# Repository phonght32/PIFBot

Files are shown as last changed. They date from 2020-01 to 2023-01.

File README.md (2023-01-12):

# PIFBot
  
### 1. Overview 

PIFBot is a ROS-based mobile robot for running SLAM (Simultaneous Localization and Mapping) algorithms to build a map and driving around this map. This robot is primarily equiped LiDAR, RGB-D camera and odometer sensors that makes it compatible with many SLAM methods. The PIFBot can be customized in various ways depending on how you reconstruct mechanical parts and use optional parts such as sensors and the computer to meet many different purposes. 

### 2. Requirement

#### 2.1. Ubuntu 16.04 Xenial
Ubuntu has been the primary platform for ROS. The releases is available to download from [Ubuntu home page.](https://ubuntu.com/)

#### 2.2. ROS Kinetic
This project uses ROS Kinetic that compatible with Ubuntu 16.04 (Xenial) to have better support from ROS community. Follow this [link](http://wiki.ros.org/kinetic) to see the installation instructions. 

#### 2.3. STM-IDF (STM32 Integrated Developement Framework)
[STM-IDF](https://github.com/phonght32/stm-idf) is an open source framework for STM32 that using C/C++ programming languague. The majority of the components in STM-IDF are available in [Github Repository](https://github.com/phonght32) under the MIT license. 

### 3. Mobile base control

Main controller board for PIFBot is OpenSTM32. The OpenSTM32 board is developed for ROS embedded systems to provide completely open source hardware and software. Everything about the board; Schematic, PCB Gerber, BOM and the firmware source code for PIFBot are available in [Github Repository](https://github.com/phonght32/openSTM32F4_LQFP64) and free to distribute under MIT license. 

The STM32F4 series is a main chip inside the OpenSTM32 board which is based on a very powerful ARM Cortex-M4 with Floating Point Unit (FPU). The developement environment for OpenSTM32 is wide open but STM-IDF which mentioned above is selected as main programming tool. 

OpenSTM32 provides digital and analog input/output pins that can interface with extension board or various sensors. 9-DOF IMU MPU9250 is available to make this board capable of processing complex motion fusion algorithms. OpenSTM32 features various communication interfaces: SPI, I2C, UART, I2S for other embedded devices. 

OpenSTM32 will be the best solution for implementing your embedded control design.

#### 3.1. Schematic
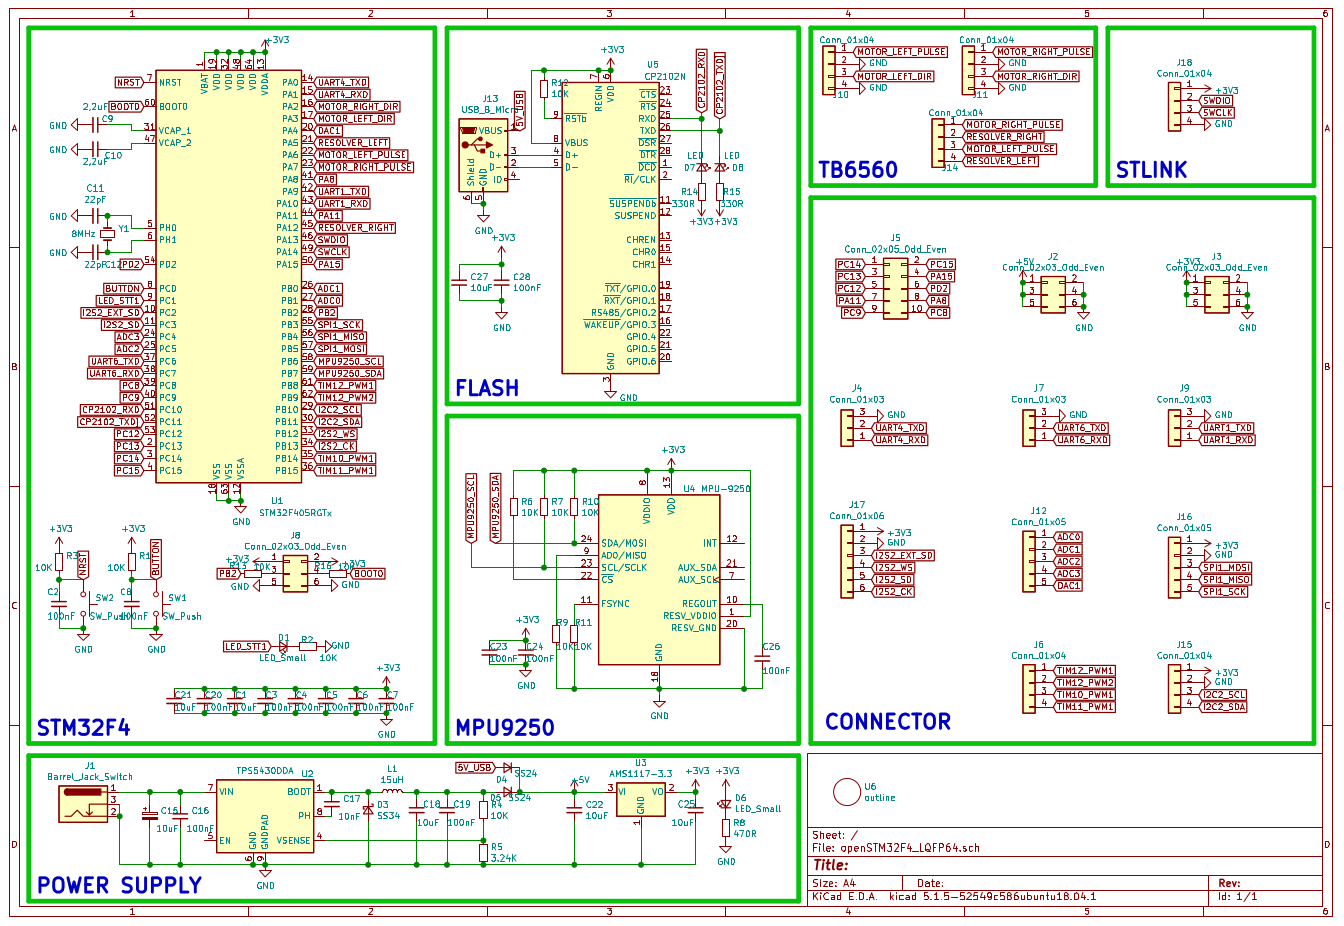
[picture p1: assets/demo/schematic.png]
schematic


#### 3.2. openSTM32 Board
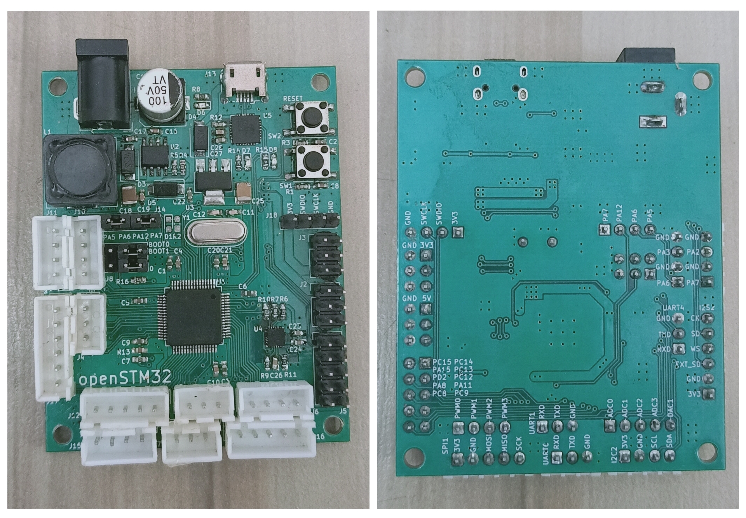
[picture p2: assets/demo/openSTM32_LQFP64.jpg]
openSTM32_LQFP64
 

### 4. Hardware assembly

Differential drive which is the most common mobile robot model is applied to PIFBot. The shape of the robot is selected as circle with two driving wheels and two caster wheels. Design in this way make the robot easy to move according to control commands. 

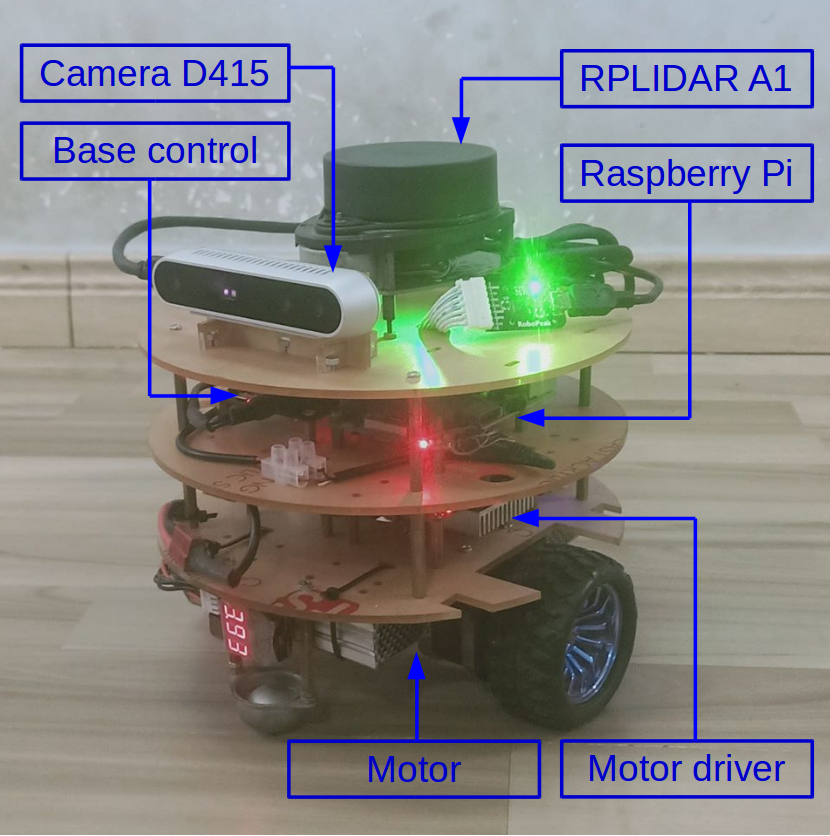
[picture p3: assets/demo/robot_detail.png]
robot_detail


This table shows many important size specifications of PIFBot. 

| Specification | Dimension |
|---|---|
| Chassis diameter | 200 mm |
| Maximum height | 212 mm |
| Wheel diameter | 65 mm |
| Axle distance | 165 mm |

#### 4.1. Chassis
PIFBot's chassis is made of mica. The chassis is designed in the way so that make it easy to carry optional parts as well as sensors. DXF files is available in this repository for laser cutting or CNC.

#### 4.2. Motor control and wheels
TB6560 stepper motor driver is used for controlling 42x42 mm stepper motor which working as actuator element. The PIFBot consists of two 65mm diameter fixed powered wheels mounted on the left and right side of the robot platform. Two castor wheels is used for balance and stability. 

#### 4.3. Single Board Computer
The Single Board Computer (SBC) is required to be able to install Linux ROS that provides the ability to use PIFBot's feature. There are various type of SBC, but Raspberry Pi 3 B+ is selected as main computer for PIFBot. 

#### 4.4. Controller Board
Calculating odometry data and controlling robot's motion are the essential requirements of controller board. The OpenSTM32 is designed to meet this requirements. There are also many available connectors in this board that make it suitable for various sensors or other applications. 

#### 4.5. Sensors
**RPLIDAR A1**  
360 Laser Range Finding RPLIDAR A1 is a 2D laser scanner capable of sensing 360 degrees that collects a set of data around the robot to use for SLAM (Simultaneous Localization and Mapping) and Navigation. It supportsnUSB interface and is easy to install on a PC. 

**Intel RealSense D415**  
The Intel RealSense D415 camera is a USB 3.0 device that can provide color, depth and infrared video streams. PIFBot adopts this camera to enable 3D SLAM and Navigation, and it is possible to apply various applications such as gesture recognition, object recognition and scene recognition based on 3D depth information obtained using RealSense Tecnology. 

#### 4.6. Power supply
OpenSTM32 controller board has both a 5V power and a 12V power, which are used in Raspberry Pi. DC/DC Buck Converter LM2596 is used for taking 11.1V from 3 cell lipo baterry and converting it into 5V that can power controller board and SBC.

### 5. System design

The system is seperated into two parts: ROS and base control. SBC receives data that collected from RPLIDAR A1 and Intel RealSense D415 camera to publish to ROS's topics. ROS's topics are owned by ROS Master so PC also implement publisher and subscriber to topics which contains data published from SBC. PC runs SLAM algorithms and Navigation, then publish motion commands to topic that manages robot's velocity (both angular and linear velocity). The motion command will be sent to controller board over rosserial protocol so that robot can build the map and drive around in this map. Simultaneously, controller board calculates robot's odometry data and feeds backward to ROS Server.

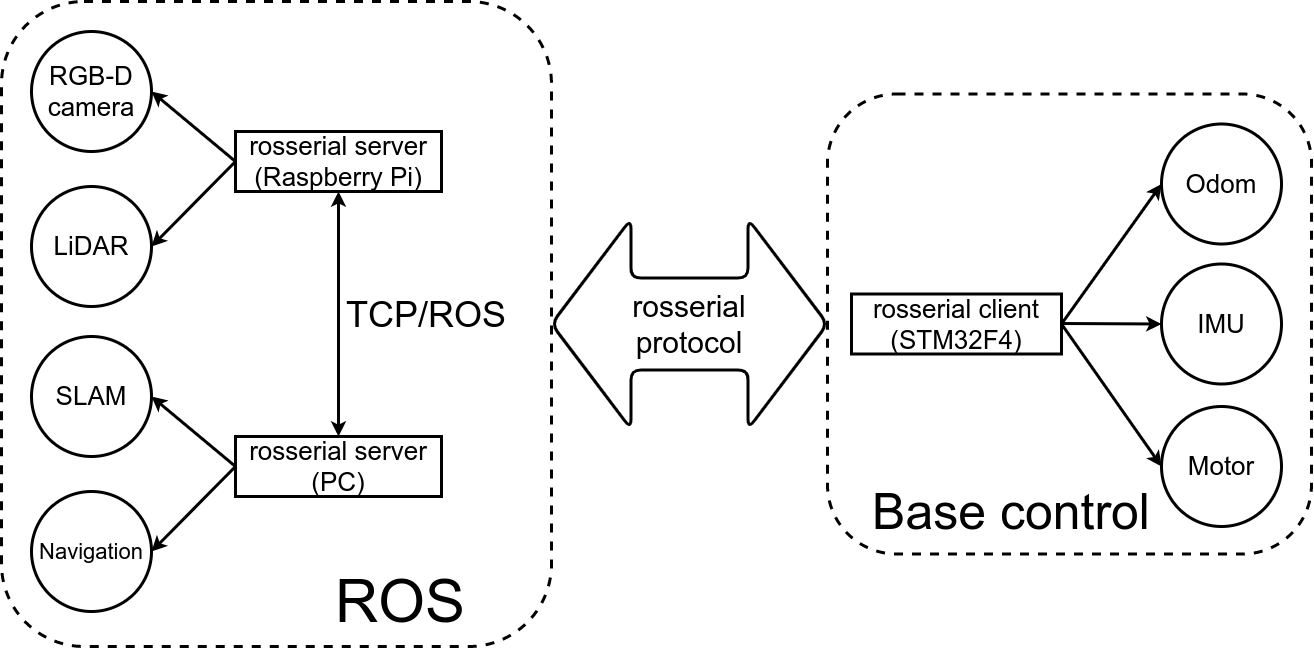
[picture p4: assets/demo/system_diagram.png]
system_diagram


### 6. Result
Real-Time Appearance-Based Mapping is used for practing SLAM and Navigation. 

#### 6.1. SLAM
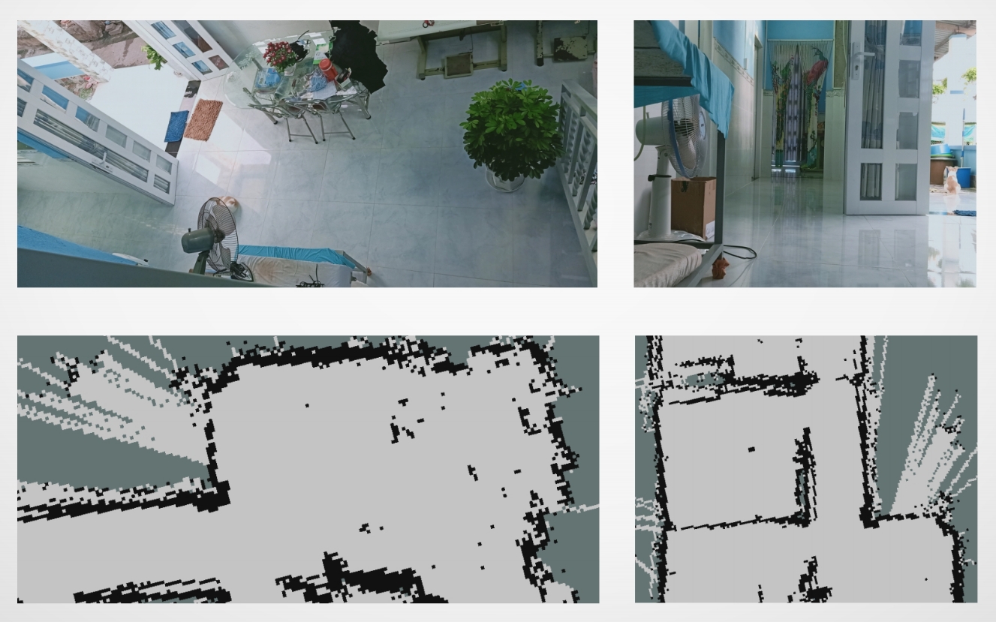
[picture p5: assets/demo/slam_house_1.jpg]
slam_house_1

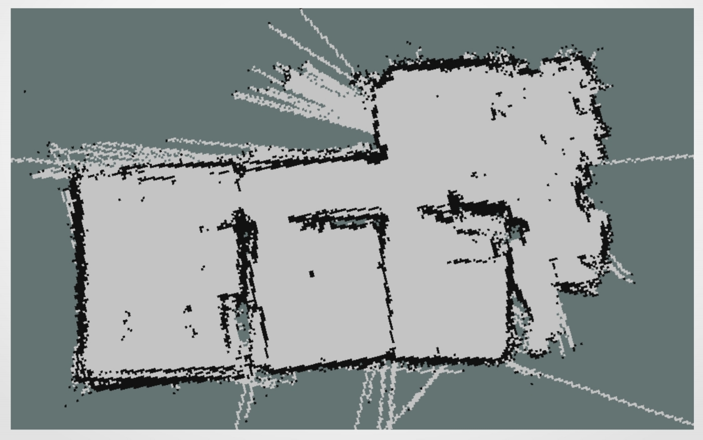
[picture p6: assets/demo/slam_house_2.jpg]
slam_house_2


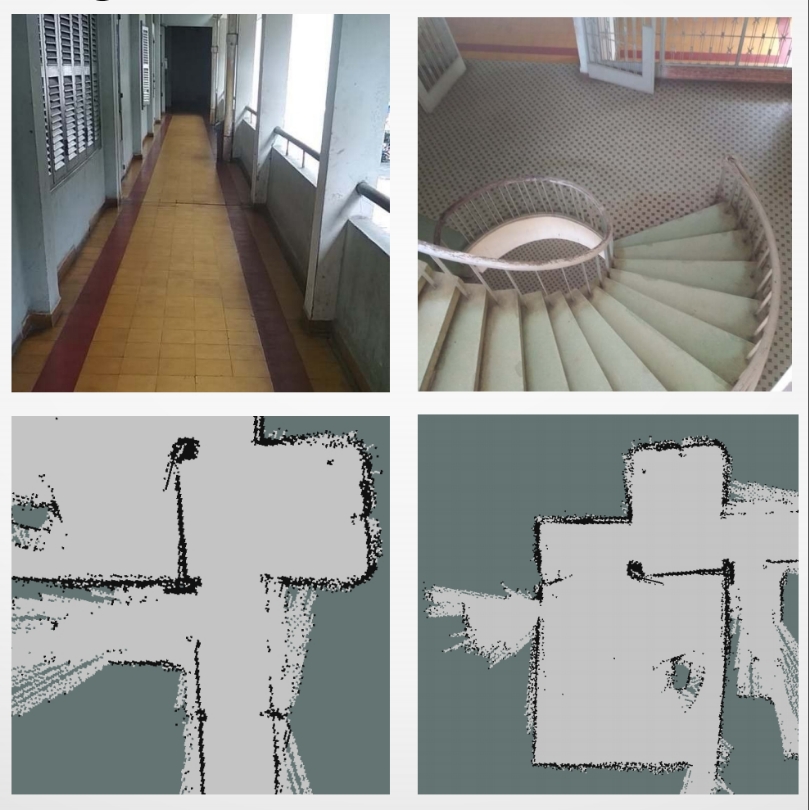
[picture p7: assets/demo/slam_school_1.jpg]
slam_school_1

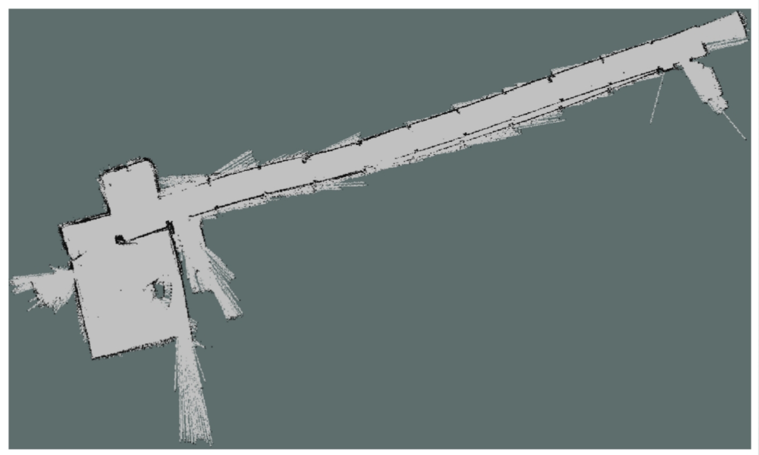
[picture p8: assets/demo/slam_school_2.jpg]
slam_school_2


#### 6.2. Navigation
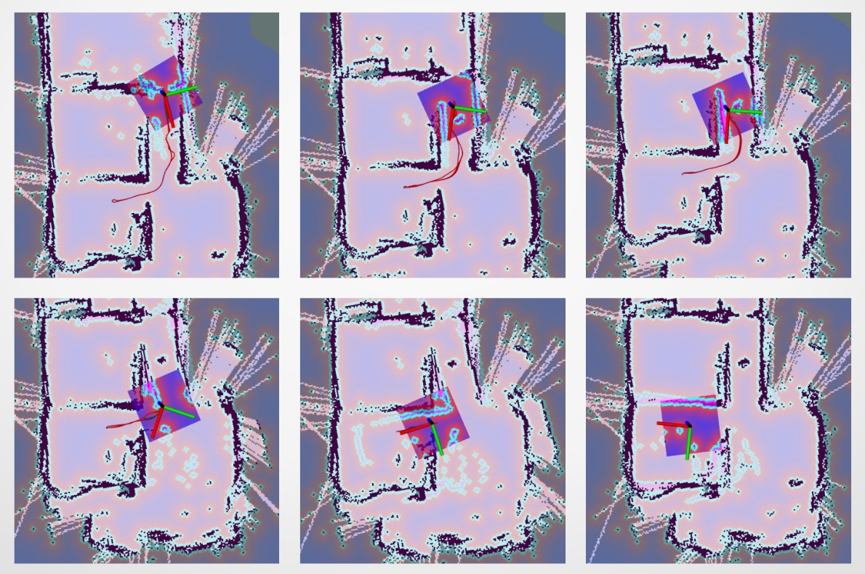
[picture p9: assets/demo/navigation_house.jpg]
navigation_house


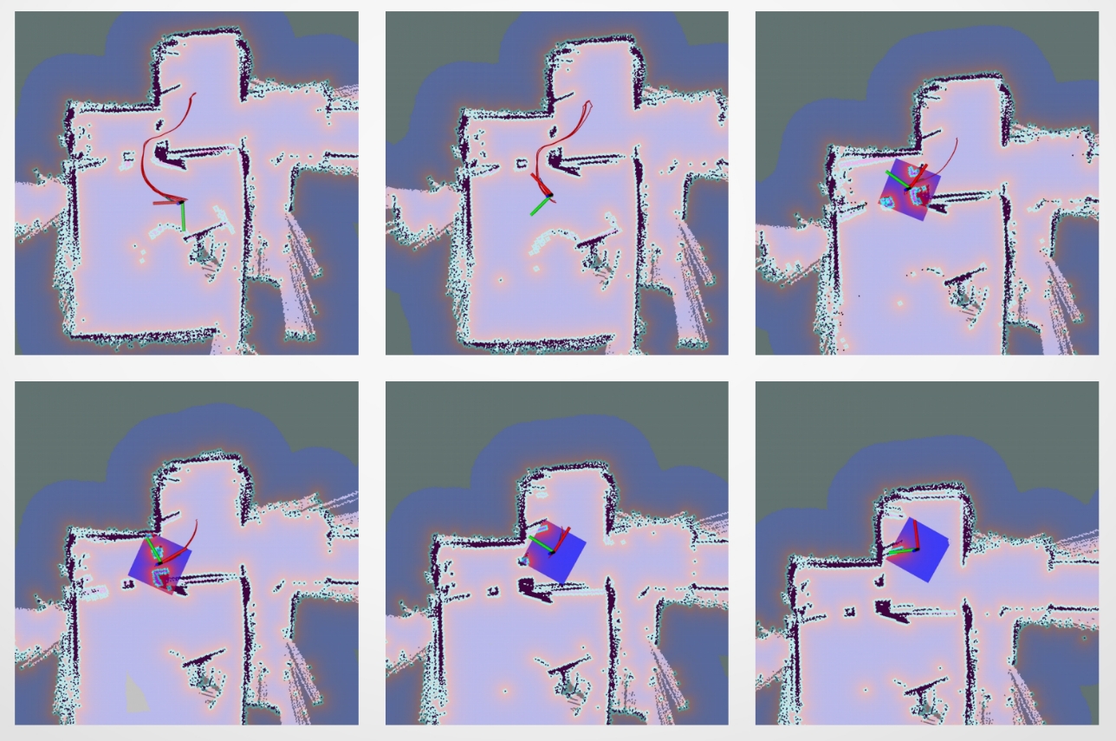
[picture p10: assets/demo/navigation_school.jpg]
navigation_school


#### 6.3. Loop-closed detection
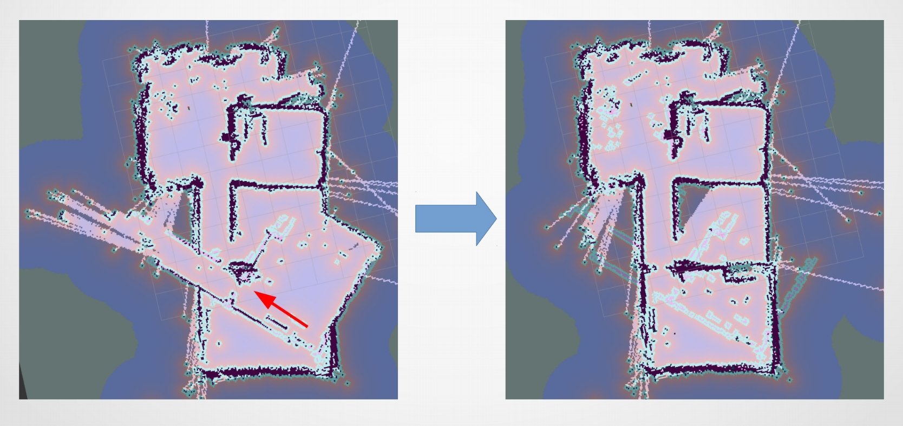
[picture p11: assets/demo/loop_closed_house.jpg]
loop_closed_house


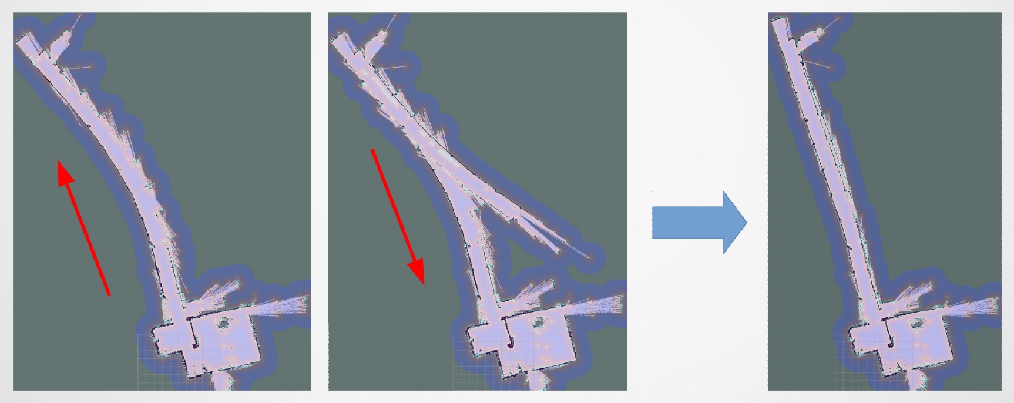
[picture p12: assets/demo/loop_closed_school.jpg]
loop_closed_school


#### 6.4. Multi-session SLAM 
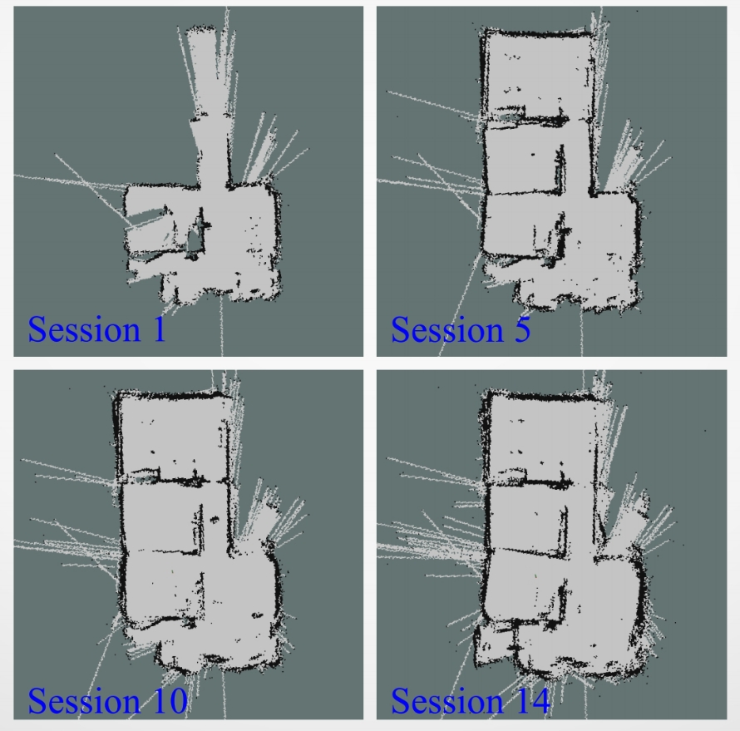
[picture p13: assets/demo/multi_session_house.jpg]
multi_session_house


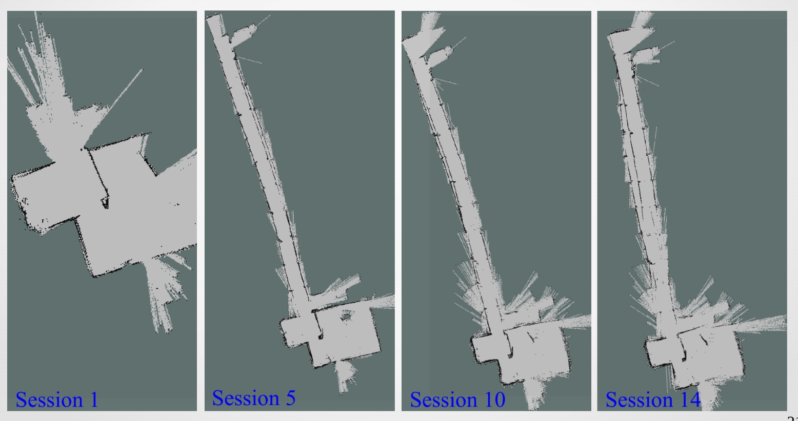
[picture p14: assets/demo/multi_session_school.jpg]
multi_session_school


#### 6.5 Video
Follow [this link](https://youtu.be/UWhPCQyU918) to watch video on Youtube. 

#### 7. Problem
For any problems, please report to [Issues](https://github.com/phonght32/PIFBot/issues) or contact email thanhphongho1998@gmail.com

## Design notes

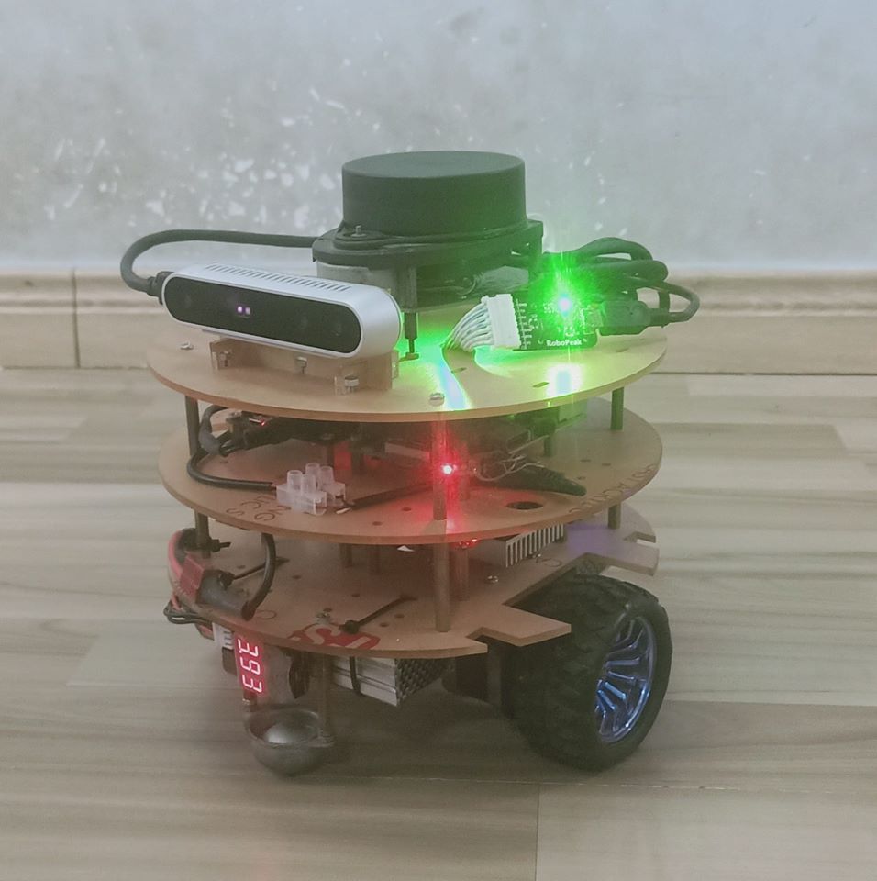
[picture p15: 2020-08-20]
assets/demo/real_robot.jpg

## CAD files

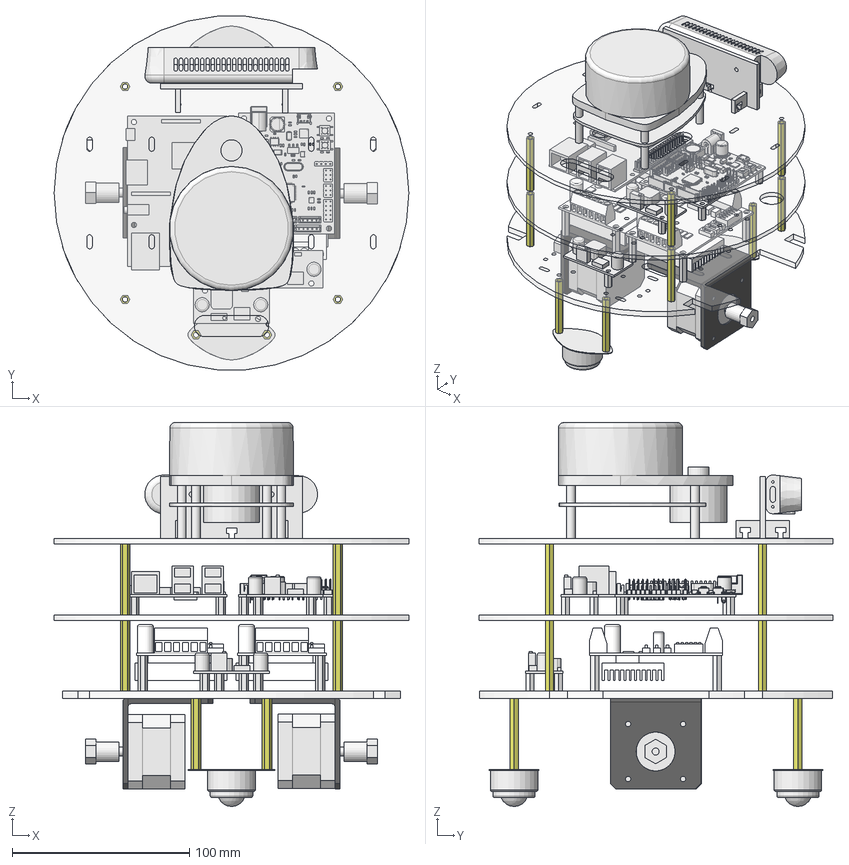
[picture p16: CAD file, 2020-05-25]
mechanical/assembly/robot_base.fcstd
200.0 x 199.3 x 216.5 mm
layer1_01
step_motor_42mm_01
step_motor_42mm_02
step_motor_42mm_bracket_01
step_motor_42mm_bracket_02
motor_flexible_coupling_connector_L18_M5_01
motor_flexible_coupling_connector_L18_M5_02
coxial_M3_40mm_01
coxial_M3_40mm_02
coxial_M3_40mm_03
coxial_M3_40mm_04
ball_transfer_01
ball_transfer_02
coxial_M3_20mm_01
coxial_M3_20mm_02
coxial_M3_20mm_03
coxial_M3_20mm_04
coxial_M3_20mm_05
coxial_M3_20mm_06
coxial_M3_20mm_07
coxial_M3_20mm_08
stepmotor_driver_tb6560_01
stepmotor_driver_tb6560_02
coxial_M3_10mm_01
coxial_M3_10mm_02
buck_converter_lm2596_01
layer2_01
coxial_M3_40mm_05
coxial_M3_40mm_06
coxial_M3_40mm_07
coxial_M3_40mm_08
coxial_M3_10mm_03
coxial_M3_10mm_04
coxial_M3_10mm_05
coxial_M3_10mm_06
coxial_M3_10mm_07
coxial_M3_10mm_08
coxial_M3_10mm_09
coxial_M3_10mm_10
coxial_M3_10mm_11
coxial_M3_10mm_12
buck_converter_lm2596_02
openSTM32F4_LQFP64_001
raspberry_pi_3Bplus_01
layer3_01
coxial_M3_40mm_09
coxial_M3_40mm_10
coxial_M3_40mm_11
coxial_M3_40mm_12
rplidar_a1_01
camera_holder_front_01
camera_holder_01
camera_holder_02
intel_realsense_d415_01

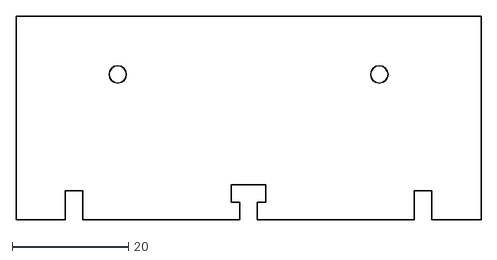
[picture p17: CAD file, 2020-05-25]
mechanical/assets/dxf/camera_holder_front.dxf
80.0 x 35.0

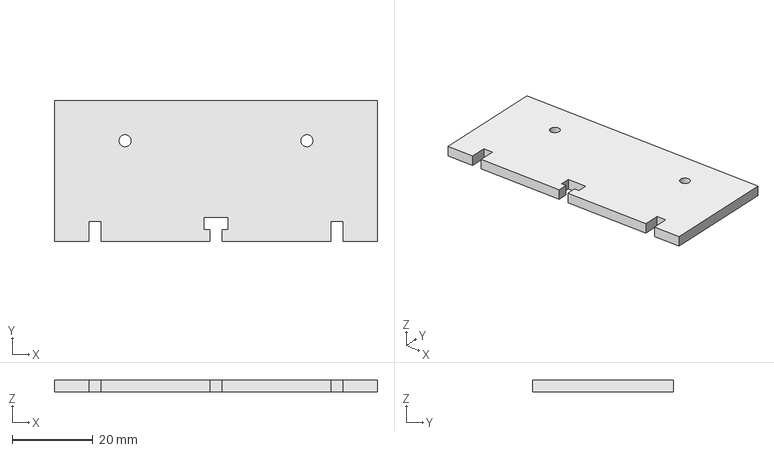
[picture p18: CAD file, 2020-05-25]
mechanical/camera_holder_front.FCStd
80.0 x 35.0 x 3.00 mm

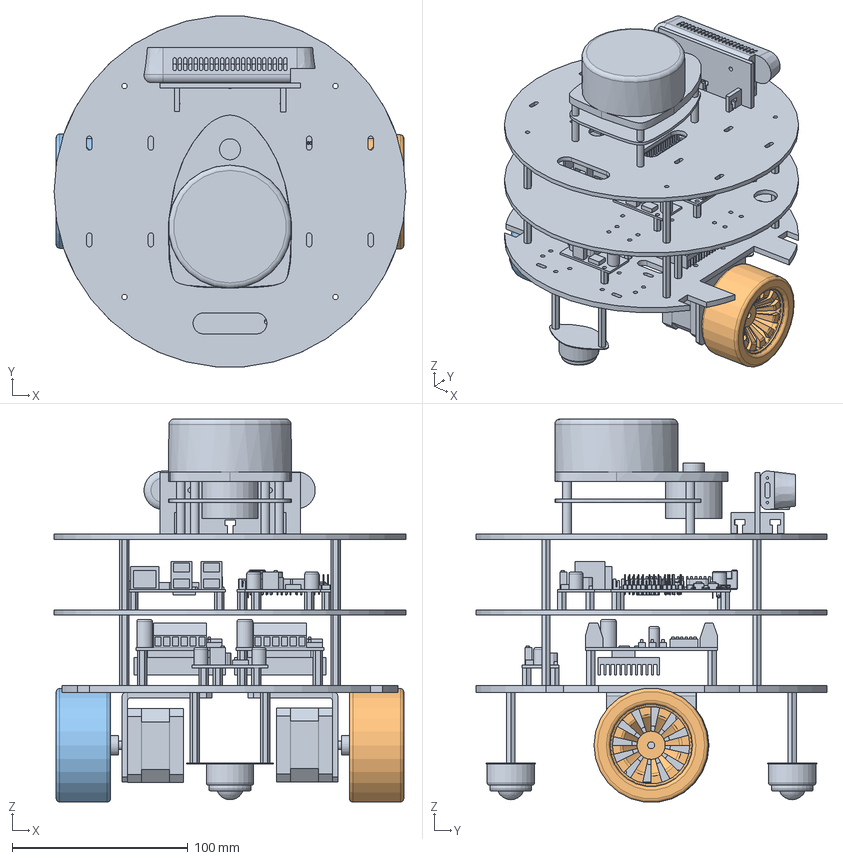
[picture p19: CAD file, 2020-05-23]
mechanical/assembly/robot.fcstd
200.0 x 199.3 x 217.8 mm
robot_base_01
robot_wheel_01
robot_wheel_02

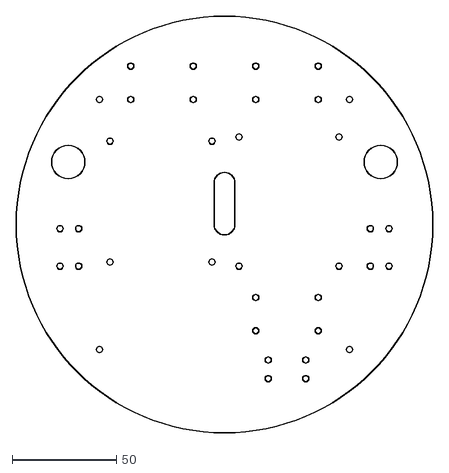
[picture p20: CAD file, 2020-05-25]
mechanical/assets/dxf/layer2.dxf
200.0 x 200.0

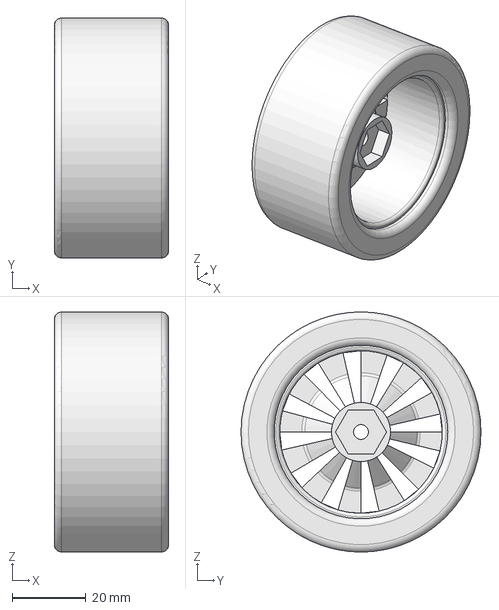
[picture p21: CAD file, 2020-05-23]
mechanical/assembly/robot_wheel.fcstd
31.0 x 65.0 x 65.0 mm

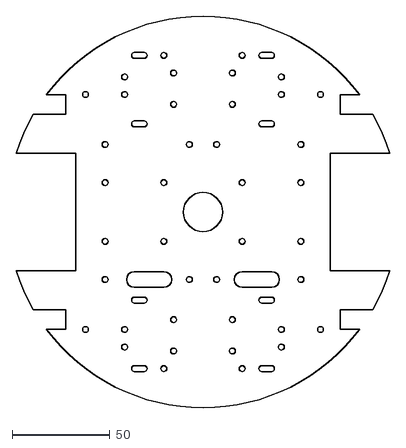
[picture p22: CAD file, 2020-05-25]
mechanical/assets/dxf/layer1.dxf
190.8 x 200.0

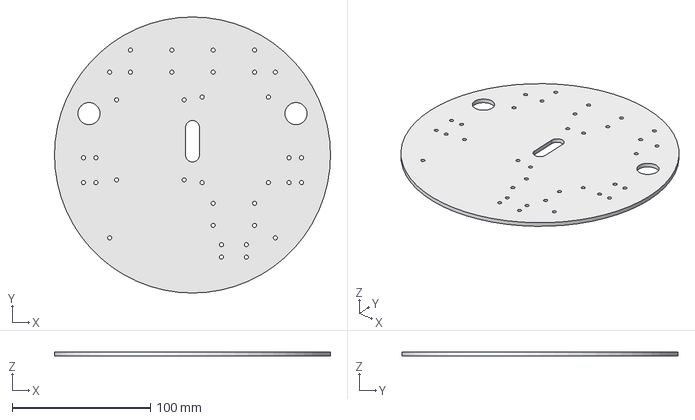
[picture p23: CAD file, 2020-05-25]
mechanical/layer2.FCStd
200.0 x 200.0 x 3.00 mm

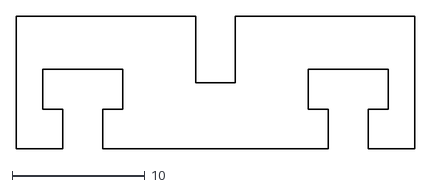
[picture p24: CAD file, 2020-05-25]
mechanical/assets/dxf/camera_holder.dxf
30.0 x 10.0

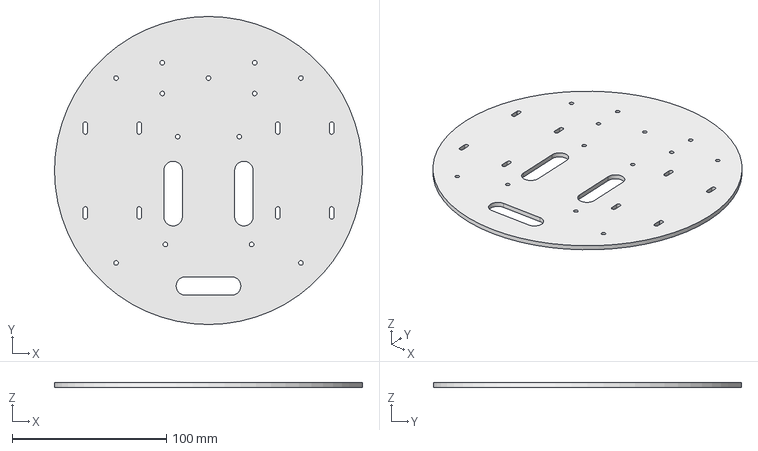
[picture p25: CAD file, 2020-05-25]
mechanical/layer3.FCStd
200.0 x 200.0 x 3.00 mm

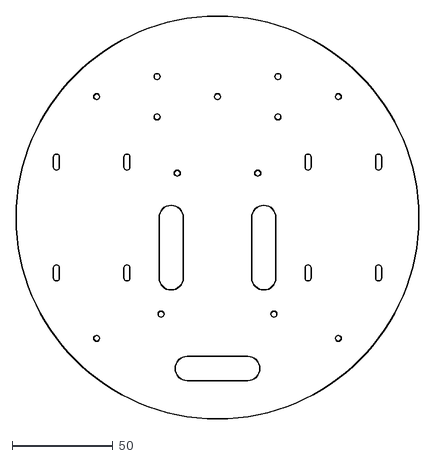
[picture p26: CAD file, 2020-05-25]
mechanical/assets/dxf/layer3.dxf
200.0 x 200.0

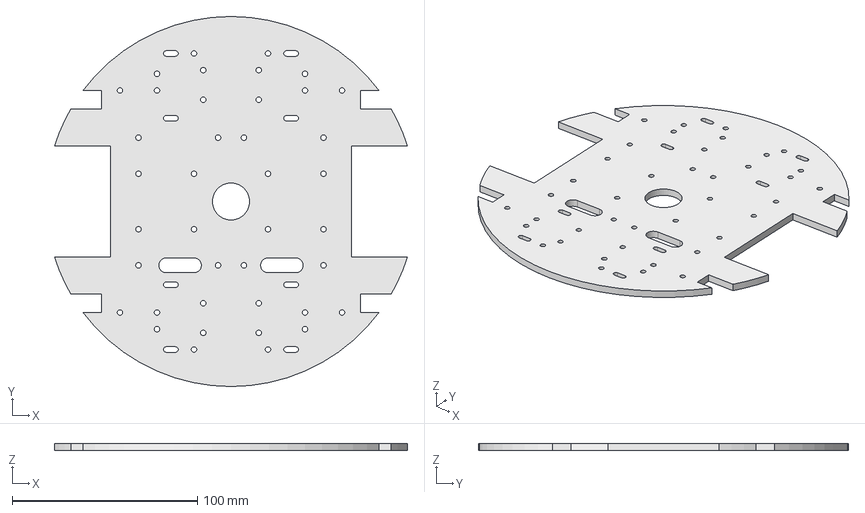
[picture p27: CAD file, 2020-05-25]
mechanical/layer1.FCStd
190.8 x 200.0 x 4.00 mm

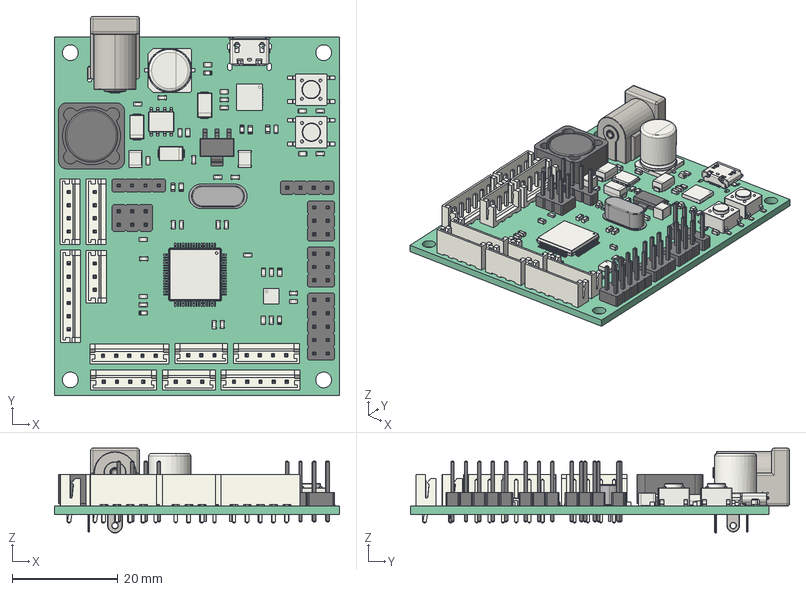
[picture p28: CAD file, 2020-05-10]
mechanical/openSTM32F4_LQFP64.FCStd
54.0 x 71.9 x 16.1 mm
Pcb_d8e2
J1_User Library-K375A -PCM DC Power Jack 2mm Pin_5EA4031C
J5_PinHeader_2x05_P254mm_Vertical_5EB08CC2
J18_PinHeader_1x04_P254mm_Vertical_5EB0AE7D
R16_R_0603_1608Metric_5EAFAF91
R13_R_0603_1608Metric_5EAFF99B
U4_QFN-24-1EP_3x3mm_Pitch0.4mm_5EA5C3D2
J3_PinHeader_2x03_P254mm_Vertical_5EA40313
J2_PinHeader_2x03_P254mm_Vertical_5EA402F7
J9_JST_B3B_EH_A_5EA3E20C
J7_JST_B3B_EH_A_5EA3E1B5
J4_JST_B3B_EH_A_5EA3E114
J14_PinHeader_1x04_P254mm_Vertical_5EAC9FAF
J8_PinHeader_2x03_P254mm_Vertical_5EAAB127
C21_C_0603_1608Metric_5EA43EF0
D4_D_SMA_5EA284CE
D3_D_SMA_5EB50787
D5_D_SMA_5EA30606
Y1_Crystal_HC49-4H_Vertical_5EA9EA10
C18_C_1210_3225Metric_5EA436E9
C25_C_1210_3225Metric_5EA31A7E
C15_CP_Elec_8x10_5EA2560F
J13_USB_Micro-B_Molex_47346-0001_5EA50851
U5_QFN-28-1EP_5x5mm_Pitch0.5mm_5EA4E590
U3_SOT_223_5EA53A3F
U2_HTSOP_8_1EP_39x49mm_Pitch127mm_5EA0849D
U1_LQFP_64_10x10mm_P05mm_5EA24989
SW2_SW_SPST_PTS645_5EB7520E
SW1_SW_SPST_PTS645_5EA3CB54
R15_R_0603_1608Metric_5EA083D6
R14_R_0603_1608Metric_5EA083C5
R12_R_0603_1608Metric_5EA4105A
R11_R_0603_1608Metric_5EA24C1D
R10_R_0603_1608Metric_5EA5C4B6
R9_R_0603_1608Metric_5EA2483F
R8_R_0603_1608Metric_5EA9B3FB
R7_R_0603_1608Metric_5EA5C456
R6_R_0603_1608Metric_5EA5C378
R5_R_0603_1608Metric_5EA0832C
R4_R_0603_1608Metric_5EA0831B
R3_R_0603_1608Metric_5EA0830A
R2_R_0603_1608Metric_5EAD2415
R1_R_0603_1608Metric_5EA082E8
L1_L_Wuerth_MAPI_3012_5EA24663
L1_SRR1260_5EA24663[2]
J17_JST_B6B_EH_A_5EA2A89C
J16_JST_B5B_EH_A_5EA0824F
J15_JST_B4B_EH_A_5EA0822C
J12_JST_B5B_EH_A_5EA3C541
J11_JST_B4B_EH_A_5EA26EEF
J10_JST_B4B_EH_A_5EA0819C
J6_JST_B4B_EH_A_5EA08116
D8_LED_0603_1608Metric_5EB538CC
D7_LED_0603_1608Metric_5EA08010
D6_LED_0603_1608Metric_5EA9B42D
D1_LED_0603_1608Metric_5EA07F8A
C28_C_0603_1608Metric_5EA4F23B
C27_C_0603_1608Metric_5EA4F26B
C26_C_0603_1608Metric_5EA24BED
C24_C_0603_1608Metric_5EA83DF3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

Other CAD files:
mechanical/camera_holder.FCStd

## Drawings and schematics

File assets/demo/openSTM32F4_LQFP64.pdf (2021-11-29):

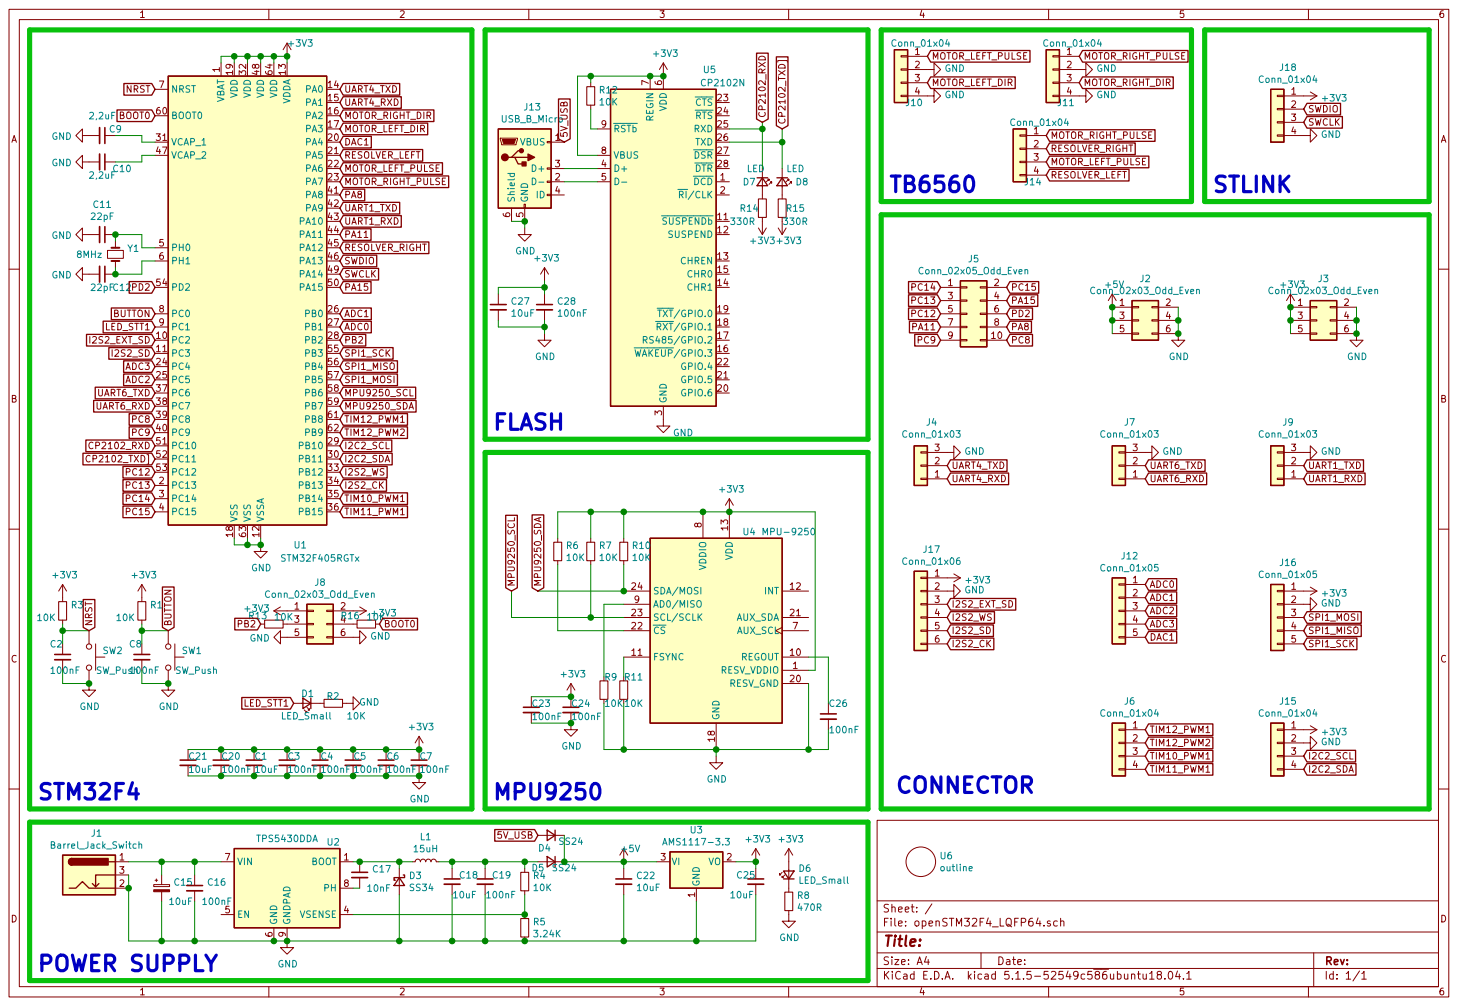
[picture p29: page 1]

1 VCAP_1 31 VCAP_2 47 VDD 19 VDD 32 VDD 48 VDD 64 VDDA 13 VSS 18 VSS 63 VSSA 12 U1 STM32F405RGTx BUTTON
PD2 BOOT0

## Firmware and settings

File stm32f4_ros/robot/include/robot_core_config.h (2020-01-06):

#ifndef _ROBOT_CORE_CONFIG_H_
#define _ROBOT_CORE_CONFIG_H_

//#include "stdint.h"

#include <ros.h>
#include <ros/time.h>
#include <std_msgs/Bool.h>
#include <std_msgs/Empty.h>
#include <std_msgs/Int32.h>
#include <std_msgs/String.h>
#include <std_msgs/UInt16.h>
#include <sensor_msgs/Imu.h>
#include <sensor_msgs/JointState.h>
#include <sensor_msgs/BatteryState.h>
#include <sensor_msgs/MagneticField.h>
#include <geometry_msgs/Vector3.h>
#include <geometry_msgs/Twist.h>
#include <tf/tf.h>
#include <tf/transform_broadcaster.h>
#include <nav_msgs/Odometry.h>

#include <robot_model_param.h>

#define CONTROL_MOTOR_SPEED_FREQUENCY          30   //hz
#define CONTROL_MOTOR_TIMEOUT                  500  //ms
#define IMU_PUBLISH_FREQUENCY                  200  //hz
#define CMD_VEL_PUBLISH_FREQUENCY              30   //hz
#define DRIVE_INFORMATION_PUBLISH_FREQUENCY    30   //hz
#define VERSION_INFORMATION_PUBLISH_FREQUENCY  1    //hz
#define DEBUG_LOG_FREQUENCY                    10   //hz

#define WHEEL_NUM                        2

#define LEFT                             0
#define RIGHT                            1

#define LINEAR                           0
#define ANGULAR                          1

#define DEG2RAD(x)                       (x * 0.01745329252)  // *PI/180
#define RAD2DEG(x)                       (x * 57.2957795131)  // *180/PI

#define TICK2RAD                         0.001533981  // 0.087890625[deg] * 3.14159265359 / 180 = 0.001533981f

#define TEST_DISTANCE                    0.300     // meter
#define TEST_RADIAN                      3.14      // 180 degree

// #define DEBUG
#define DEBUG_SERIAL                     SerialBT2


void commandVelocityCallback(const geometry_msgs::Twist& cmd_vel_msg);
void resetCallback(const std_msgs::Empty &reset_msg);

void publishCmdVelFromMotorMsg(void);
void publishImuMsg(void);
void publishDriveInformation(void);

ros::Time rosNow(void);
ros::Time addMicros(ros::Time &t, uint32_t _micros);

void updateVariable(bool isConnected);
void updateMotorInfo(int32_t left_tick, int32_t right_tick);
void updateTime(void);
void updateOdometry(void);
void updateJoint(void);
void updateJointStates(void);
void updateTF(geometry_msgs::TransformStamped& odom_tf);
void updateGyroCali(bool isConnected);
void updateGoalVelocity(void);
void updateTFPrefix(bool isConnected);

void initOdom(void);
void initJointStates(void);

bool calcOdometry(double diff_time);

void sendLogMsg(void);
void waitForSerialLink(bool isConnected);


/*******************************************************************************
* ROS NodeHandle
*******************************************************************************/
ros::NodeHandle nh;
ros::Time current_time;
uint32_t current_offset;

/*******************************************************************************
* ROS Parameter
*******************************************************************************/
char get_prefix[10];
char *get_tf_prefix = get_prefix;

char odom_header_frame_id[30];
char odom_child_frame_id[30];

char imu_frame_id[30];

char joint_state_header_frame_id[30];

/*******************************************************************************
* Subscriber
*******************************************************************************/
ros::Subscriber<geometry_msgs::Twist> cmd_vel_sub("cmd_vel", commandVelocityCallback);

ros::Subscriber<std_msgs::Empty> reset_sub("reset", resetCallback);

/*******************************************************************************
* Publisher
*******************************************************************************/
sensor_msgs::Imu imu_msg;
ros::Publisher imu_pub("imu", &imu_msg);

geometry_msgs::Twist cmd_vel_motor_msg;
ros::Publisher cmd_vel_motor_pub("cmd_vel_motor", &cmd_vel_motor_msg);

nav_msgs::Odometry odom;
ros::Publisher odom_pub("odom", &odom);

sensor_msgs::JointState joint_states;
ros::Publisher joint_states_pub("joint_states", &joint_states);

sensor_msgs::BatteryState battery_state_msg;
ros::Publisher battery_state_pub("battery_state", &battery_state_msg);

/*******************************************************************************
* Transform Broadcaster
*******************************************************************************/
geometry_msgs::TransformStamped odom_tf;
tf::TransformBroadcaster tf_broadcaster;

/*******************************************************************************
* SoftwareTimer of Robot
*******************************************************************************/
static uint32_t tTime[10];

/*******************************************************************************
* Calculation for odometry
*******************************************************************************/
bool init_encoder = true;
int32_t last_diff_tick[WHEEL_NUM] = {0, 0};
double last_rad[WHEEL_NUM] = {0.0, 0.0};
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

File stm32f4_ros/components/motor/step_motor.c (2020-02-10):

#include "include/step_motor.h"

#define PWM_DUTYCYCLE_DEFAULT	30

typedef struct step_motor {
    pwm_handle_t clk_handle;
    gpio_handle_t dir_handle;
} step_motor_t;

static void step_motor_cleanup(step_motor_handle_t handle)
{
	free(handle->dir_handle);
	free(handle->clk_handle);
	free(handle);
}

step_motor_handle_t step_motor_init(step_motor_config_t *config)
{
    step_motor_handle_t handle;
    if( (handle             = calloc(1, sizeof(step_motor_t))) &&
        (handle->clk_handle = calloc(1, sizeof(pwm_handle_t)))  &&
        (handle->dir_handle = calloc(1, sizeof(gpio_handle_t))) == NULL )
    {
    	step_motor_cleanup(handle);
        return -1;
    }

    handle->clk_handle = pwm_init(&config->pin_clk);
    handle->dir_handle = gpio_init(&config->pin_dir);
    pwm_set_duty(handle->clk_handle, PWM_DUTYCYCLE_DEFAULT);

    return handle;
}

int step_motor_start(step_motor_handle_t handle)
{
	pwm_start(handle->clk_handle);

	return 0;
}

int step_motor_stop(step_motor_handle_t handle)
{
	pwm_stop(handle->clk_handle);

	return 0;
}

int step_motor_set_freq(step_motor_handle_t handle, uint32_t freq_hz)
{
	pwm_set_freq(handle->clk_handle,freq_hz);

	return 0;
}

int step_motor_set_dir(step_motor_handle_t handle, bool dir)
{
	gpio_set_level(handle->dir_handle, dir);

	return 0;
}

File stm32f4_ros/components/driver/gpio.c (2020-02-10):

#include "include/gpio.h"

#define GPIO_SPEED_FREQ_DEFAULT  GPIO_SPEED_FREQ_VERY_HIGH

typedef struct gpio {
    gpio_port_t     gpio_port;
    gpio_num_t      gpio_num;
    gpio_mode_t     gpio_mode;
    gpio_reg_pull_t gpio_reg_pull;
} gpio_t;

GPIO_TypeDef *GPIOx_MAPPING[GPIO_PORT_MAX] = {
    GPIOA,
    GPIOB,
    GPIOC,
    GPIOD,
    GPIOE,
    GPIOF,
    GPIOG,
    GPIOH,
    GPIOI
};

uint16_t GPIO_PIN_x_MAPPING[GPIO_NUM_MAX] = {
    GPIO_PIN_0,
    GPIO_PIN_1,
    GPIO_PIN_2,
    GPIO_PIN_3,
    GPIO_PIN_4,
    GPIO_PIN_5,
    GPIO_PIN_6,
    GPIO_PIN_7,
    GPIO_PIN_8,
    GPIO_PIN_9,
    GPIO_PIN_10,
    GPIO_PIN_11,
    GPIO_PIN_12,
    GPIO_PIN_13,
    GPIO_PIN_14,
    GPIO_PIN_15
};

uint32_t GPIO_REG_PULL_MAPPING[GPIO_REG_PULL_MAX] = {
    GPIO_NOPULL,
    GPIO_PULLUP,
    GPIO_PULLDOWN
};

uint32_t RCC_AHB1ENR_GPIOxEN_MAPPING[GPIO_PORT_MAX] = {
    RCC_AHB1ENR_GPIOAEN,
    RCC_AHB1ENR_GPIOBEN,
    RCC_AHB1ENR_GPIOCEN,
    RCC_AHB1ENR_GPIODEN,
    RCC_AHB1ENR_GPIOEEN,
    RCC_AHB1ENR_GPIOFEN,
    RCC_AHB1ENR_GPIOGEN,
    RCC_AHB1ENR_GPIOHEN,
    RCC_AHB1ENR_GPIOIEN,
};

gpio_handle_t gpio_init(gpio_config_t *config)
{
    gpio_handle_t handle;
    handle = calloc(1, sizeof(gpio_t));
    if (handle == NULL)
    {
        return -1;
    }

    uint32_t RCC_AHB1ENR_GPIOxEN;
    uint16_t GPIO_PIN_x;
    GPIO_TypeDef *GPIOx;
    uint32_t GPIO_REG_PULL_TYPE;

    RCC_AHB1ENR_GPIOxEN = RCC_AHB1ENR_GPIOxEN_MAPPING[config->gpio_port];
    GPIO_PIN_x = GPIO_PIN_x_MAPPING[config->gpio_num];
    GPIOx = GPIOx_MAPPING[config->gpio_port];
    GPIO_REG_PULL_TYPE = GPIO_REG_PULL_MAPPING[config->gpio_reg_pull];

    do {
        __IO uint32_t tmpreg = 0x00U;
        SET_BIT(RCC->AHB1ENR, RCC_AHB1ENR_GPIOxEN);
        tmpreg = READ_BIT(RCC->AHB1ENR, RCC_AHB1ENR_GPIOxEN);
        UNUSED(tmpreg);
    } while (0U);

    GPIO_InitTypeDef GPIO_InitStruct = {0};
    if (config->gpio_mode == GPIO_INPUT)
    {
        GPIO_InitStruct.Pin = GPIO_PIN_x;
        GPIO_InitStruct.Mode = GPIO_MODE_INPUT;
        GPIO_InitStruct.Pull = GPIO_REG_PULL_TYPE;
        HAL_GPIO_Init(GPIOx, &GPIO_InitStruct);
    }
    if (config->gpio_mode == GPIO_OUTPUT)
    {
        HAL_GPIO_WritePin(GPIOx, GPIO_PIN_x, GPIO_PIN_RESET);
        GPIO_InitStruct.Pin = GPIO_PIN_x;
        GPIO_InitStruct.Mode = GPIO_MODE_OUTPUT_PP;
        GPIO_InitStruct.Pull = GPIO_REG_PULL_TYPE;
        GPIO_InitStruct.Speed = GPIO_SPEED_FREQ_DEFAULT;
        HAL_GPIO_Init(GPIOx, &GPIO_InitStruct);
    }

    handle->gpio_port     = config->gpio_port;
    handle->gpio_num      = config->gpio_num;
    handle->gpio_mode     = config->gpio_mode;
    handle->gpio_reg_pull = config->gpio_reg_pull;

    return handle;
}

int gpio_set_level(gpio_handle_t handle, uint8_t state)
{
    HAL_GPIO_WritePin(GPIOx_MAPPING[handle->gpio_port], GPIO_PIN_x_MAPPING[handle->gpio_num], state);

    return 0;
}

int gpio_toggle_level(gpio_handle_t handle)
{
    HAL_GPIO_TogglePin(GPIOx_MAPPING[handle->gpio_port], GPIO_PIN_x_MAPPING[handle->gpio_num]);

    return 0;
}

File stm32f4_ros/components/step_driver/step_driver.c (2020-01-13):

#include "stm32f4xx_hal.h"

#include "stdlib.h"

#include "include/step_driver.h"

#define PWM_DUTYCYCLE_DEFAULT	30

typedef struct step_driver {
    pwm_handle_t clk_handle;
    gpio_handle_t dir_handle;
} step_driver_t;

static void step_driver_cleanup(step_driver_handle_t handle)
{
	free(handle->dir_handle);
	free(handle->clk_handle);
	free(handle);
}

step_driver_handle_t step_driver_init(step_driver_config_t *config)
{
    step_driver_handle_t handle;
    if( (handle             = calloc(1, sizeof(step_driver_t))) &&
        (handle->clk_handle = calloc(1, sizeof(pwm_handle_t)))  &&
        (handle->dir_handle = calloc(1, sizeof(gpio_handle_t))) == NULL )
    {
    	step_driver_cleanup(handle);
        return -1;
    }

    handle->clk_handle = pwm_init(&config->pin_clk);
    handle->dir_handle = gpio_init(&config->pin_dir);
    pwm_set_duty(handle->clk_handle, PWM_DUTYCYCLE_DEFAULT);

    return handle;
}

int step_driver_start(step_driver_handle_t handle)
{
	pwm_start(handle->clk_handle);

	return 0;
}

int step_driver_stop(step_driver_handle_t handle)
{
	pwm_stop(handle->clk_handle);

	return 0;
}

int step_driver_set_freq(step_driver_handle_t handle, uint32_t freq_hz)
{
	pwm_set_freq(handle->clk_handle,freq_hz);

	return 0;
}

int step_driver_set_dir(step_driver_handle_t handle, bool dir)
{
	gpio_set_level(handle->dir_handle, dir);

	return 0;
}

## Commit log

2019-11-25 add freecad 3d models
    [assembly_chasis.FCStd, ball-transfer.FCStd, coxial-4cm.FCStd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]
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2019-11-27 add pwm_init() function
    [stm32f407 Debug.cfg]
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2019-11-28 fix params in struct config of pwm_init() and return type
    [timer.c]
2019-11-28 fix pwm_init() return value
    [timer.c]
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2019-11-28 fix pwm_start()
2019-11-28 fix pwm_set_timer_params() argument
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2019-11-28 fix TIM_OCxInit in pwm_init() function
    [timer.c]
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2019-12-01 fix HSE_VALUE in stm32f4xx.h
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2019-12-04 add dma init & dma intr enable function
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2019-12-11 fix a4988 handle structure
    [timer.c]
2019-12-16 add kicad component
    [mainboard.kicad_pcb, mainboard.sch]
2019-12-16 remove kicad mainboard project
    [mainboard.kicad_pcb, mainboard.sch]
2019-12-16 add gazebo
    [model.sdf]
2019-12-16 update 3d model
    [assembly_chasis.FCStd, model.sdf, robot_base.FCStd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]
2019-12-17 update kicad project
    [mainboard.kicad_pcb, mainboard.sch]
2019-12-17 update freecad model.sdf
    [model.sdf]
2019-12-18 update robot model
    [model.sdf, robot_base.stl, robot_wheel.stl]
2019-12-18 add turtlebot3
    [model.sdf, robot_base.stl, robot_wheel.stl]
2019-12-18 update model urdf
    [assembly_chasis.FCStd, common_properties.xacro, lds.stl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]
2019-12-18 add robot teleop
    [robot_thesis_v1_0.urdf.xacro]
2019-12-18 remove param robot model
    [robot_thesis.gazebo.xacro, robot_thesis.urdf.xacro]
2019-12-21 complete pcb
    [mainboard.kicad_pcb, mainboard.sch, mainboard_v1_0.kicad_pcb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]
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2019-12-24 fix stm rosserial
    [layer1.FCStd, mainboard_v1_0.kicad_pcb]
2019-12-25 add stm32f4 hal custom lib
    [layer1.FCStd, layer1.dxf, layer2.FCStd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]
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2019-12-28 add stm32f4 ros
    [stm32f4_hal_ros Debug.cfg]
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2019-12-28 update ros
    [stm32f407 Debug.cfg]
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2019-12-31 update uart check error
    [uart.c]
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2020-01-03 add stm32f4 project
    [stm32f4 Debug.cfg, stm32f4_hal_ros Debug.cfg]
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2020-01-07 add ros time now
    [stm32f4_ros Debug.cfg]
2020-01-09 add diode & led status
    [mainboard_v1_0.kicad_pcb, mainboard_v1_0.sch]
2020-01-13 update schematic
    [mainboard_v1_0.kicad_pcb, mainboard_v1_0.sch]
2020-01-19 fix hardware
    [mainboard_v1_0.kicad_pcb]
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2020-02-08 update robot_base model
    [assembly_chasis.FCStd, robot_base.FCStd, robot_base.stl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]
2020-02-08 update urdf description
    [lds.stl, left_tire.stl, right_tire.stl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]
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2020-02-10 remove stm32f4 project
    [stm32f4 Debug.cfg, stm32f4_hal_ros Debug.cfg]
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2020-02-10 add project file
    [mainboard_v2_0.kicad_pcb, mainboard_v2_0.sch]
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2020-03-01 fix get imu quaternion
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2020-03-08 update imu filter and fix imu sensor function
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2020-03-20 remove lidar-camera submodule
    [LidarCam.cfg]
2020-03-20 remove submodule
    [LidarCam.cfg, dynamic_range.cfg]
2020-03-20 remove submodule file
    [dynamic_range.cfg]
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2020-03-23 add camera simulation
    [robot_thesis.gazebo.xacro, robot_thesis.urdf.xacro]
2020-04-02 change robot footprint
    [robot_thesis.gazebo.xacro]
2020-04-02 fix collision in urdf description
    [robot_thesis.urdf.xacro]
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2020-04-12 fix error cannot run imu
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2020-04-21 remove stm32 firmware used sw4stm32
    [stm32f4_ros Debug.cfg]
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2020-04-21 remove hardware v2.0 folder
    [mainboard_v2_0.kicad_pcb, mainboard_v2_0.sch]
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2020-04-26 change robot simulation folder name
    [model.sdf, robot_base.stl, robot_lidar.stl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]
2020-04-27 fix error when update timer macros
2020-05-01 add dqn
    [model.sdf]
2020-05-02 update gazebo sim path of models
    [model-1_4.sdf, model.sdf]
2020-05-02 change plugin name
    [robot_thesis.gazebo.xacro]
2020-05-02 add camera
    [robot_thesis.gazebo.xacro, robot_thesis.urdf.xacro]
2020-05-02 change image topic name
    [robot_thesis.gazebo.xacro]
2020-05-03 add 2 mono camera
    [robot_thesis.gazebo.xacro, robot_thesis.urdf.xacro]
2020-05-03 add model collision
    [robot_thesis.urdf.xacro]
2020-05-03 update body collision
    [robot_thesis.urdf.xacro]
2020-05-04 change camera topics
    [robot_thesis.gazebo.xacro]
2020-05-04 change camera position
    [robot_thesis.urdf.xacro]
2020-05-04 add house simulation
    [model.sdf]
2020-05-05 add stereo camera
    [robot_thesis.gazebo.xacro, robot_thesis.urdf.xacro]
2020-05-05 add rtabmap
    [webcam_calibration.yaml]
2020-05-06 remove stereo visual
    [robot_thesis.urdf.xacro]
2020-05-07 add camera optical frames
    [robot_thesis.gazebo.xacro, robot_thesis.urdf.xacro]
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2020-05-07 remove old board hardware
    [mainboard_v1_0.kicad_pcb, mainboard_v1_0.sch]
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2020-05-07 remove old ros packages
    [common_properties.xacro, model-1_4.sdf, model.sdf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]
2020-05-07 rename folder mechanical
    [assembly_chasis.FCStd, ball-transfer.FCStd, coxial-4cm.FCStd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]
2020-05-08 add freecad lib
    [ball-transfer.FCStd, coxial-4cm.FCStd, coxial-5cm.FCStd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]
2020-05-08 add assets
    [layer1.dxf, layer2.dxf, layer3.dxf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]
2020-05-09 update assembly
    [assembly_chasis.FCStd, assembly_robot.FCStd]
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2020-05-12 update extension hole
    [asembly_layer2.FCStd, assembly_robot.FCStd, layer1.FCStd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]
2020-05-12 complete mechanical
    [assembly_robot.FCStd, layer2.FCStd, layer3.FCStd]
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2020-05-18 add render
    [assembly_robot.FCStd]
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2020-05-19 update layer2
    [assembly_robot.FCStd, layer2.FCStd]
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2020-05-22 add camera holder
    [camera_holder.FCStd, camera_holder_front.FCStd]
2020-05-22 change lidar and camera hole position
    [layer3.FCStd]
2020-05-22 update dxf file
    [camera_holder.dxf, camera_holder_front.dxf, layer1.dxf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]
2020-05-22 create 2d shape to export dxf
    [camera_holder.FCStd, camera_holder_front.FCStd, layer1.FCStd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]
2020-05-23 add assembly
    [robot_base.fcstd, robot_wheel.fcstd]
2020-05-23 remove unused assembly file
    [assembly_robot.FCStd]
2020-05-25 update export dxf file
    [camera_holder.FCStd, camera_holder.dxf, camera_holder_front.FCStd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]
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2020-06-01 fix error when set pwm frequency equal zero
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2020-06-04 run rtabmap basic (only depth camera, without odom and lidar
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2020-06-07 fix odometry error when motor tick overflow
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2020-06-29 fix error when set pwm frequency of step motor
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2020-07-19 remove unused file in mechanical
    [model_v1_0.sdf, robot_base.stl, robot_wheel.stl]
